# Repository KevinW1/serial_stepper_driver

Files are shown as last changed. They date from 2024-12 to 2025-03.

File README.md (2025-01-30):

# serial_stepper_driver
Simple stepper motor driver that can be controlled via serial communication.

Most existing drivers I found did not support 3 switch or analog inputs, so I created this.

Mouser parts:
https://www.mouser.com/ProjectManager/ProjectDetail.aspx?AccessID=6cd5e76669

Micro:
https://www.pjrc.com/store/teensy40.html

Driver:
https://www.pololu.com/product/3768

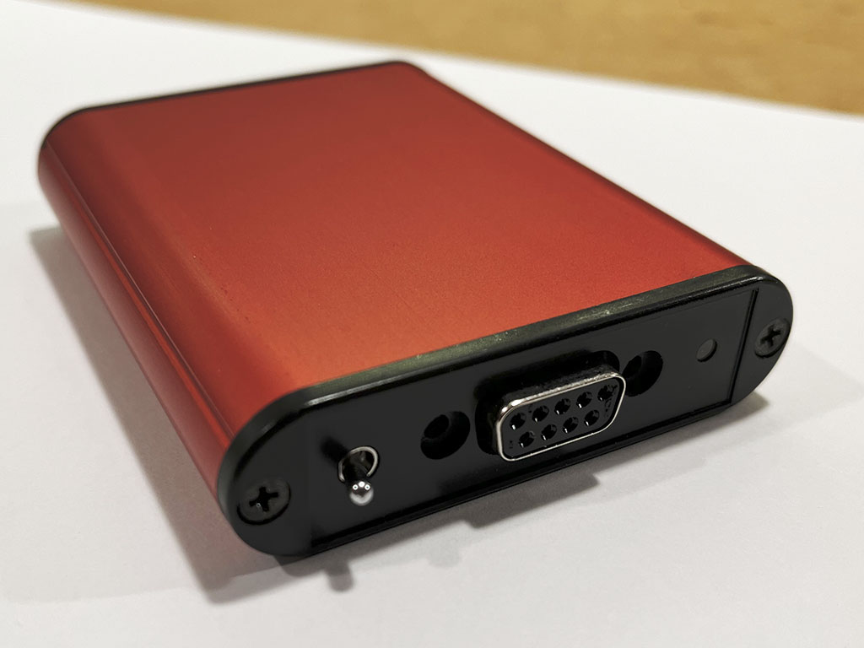
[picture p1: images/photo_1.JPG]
Finished Assembly
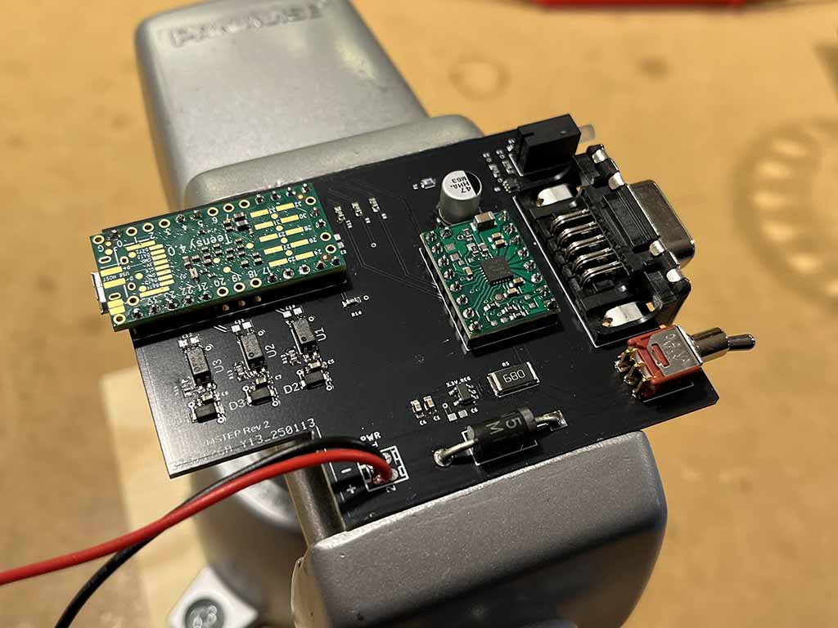
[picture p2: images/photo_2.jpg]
Board
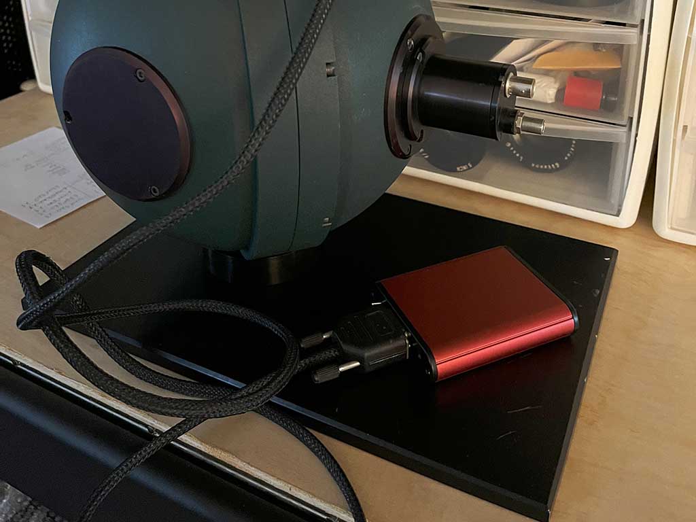
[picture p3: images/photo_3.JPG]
Application
|  |  |  |
|---|---|---|

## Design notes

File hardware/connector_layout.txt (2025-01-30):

1 B1
2 B2
3 A2
4 A1
5 GND
6 PWR (opto, hall sensor)
7 Lim1
8 Lim2
9 Home

gnd A1  A2  B1  B2
5   4   3   2   1
  6   7   8   9
  3.3 L1  L2  Home

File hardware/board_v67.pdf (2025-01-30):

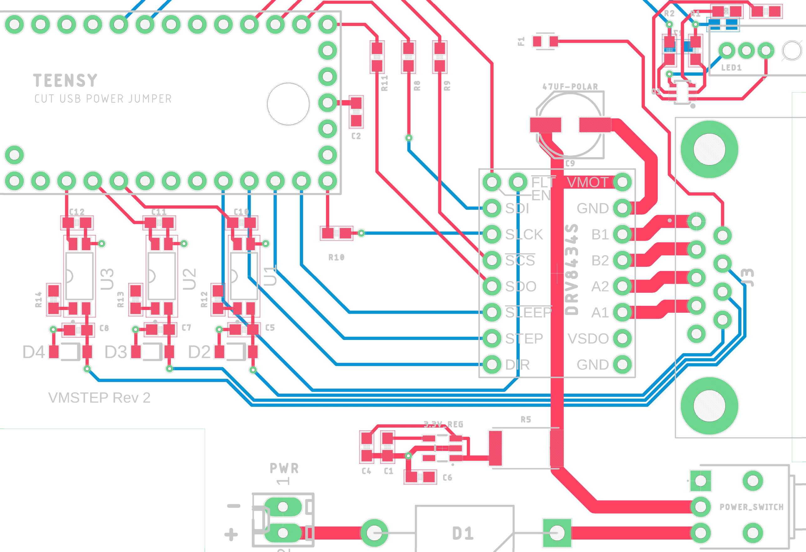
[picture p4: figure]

2

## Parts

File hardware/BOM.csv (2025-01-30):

SERIAL STEPPER DRIVER
https://www.mouser.com/ProjectManager/ProjectDetail.aspx?AccessID=6cd5e76669
Mouser # | Mfr. # | Manufacturer | Description | Order Qty. | Price (USD) | Ext.: (USD)
279-352268RJT | 352268RJT | TE Connectivity | Thick Film Resistors - SMD 3522 68R 5% 3W | 1 | $0.82 | $0.82
757-TLP291GBSE | TLP291(GB,SE | Toshiba | Transistor Output Optocouplers Gen Purp 1-Circuit 50mA 80V 3750Vrms | 3 | $0.48 | $1.44
576-SMF3.3 | SMF3.3 | Littelfuse | ESD Protection Diodes / TVS Diodes 200W 3.3V 5% Uni-directional | 3 | $0.45 | $1.35
80-C0603C104K5RAUTO | C0603C104K5RACAUTO | KEMET | Multilayer Ceramic Capacitors MLCC - SMD/SMT 50V 0.1uF X7R 0603 10% AEC-Q200 | 4 | $0.11 | $0.44
603-RC0603FR-07220RL | RC0603FR-07220RL | YAGEO | Thick Film Resistors - SMD 220 Ohms 100mW 0603 1% | 5 | $0.10 | $0.50
530-C2Q250 | C2Q 250 | Bel | Surface Mount Fuses Fuse | 2 | $0.29 | $0.58
603-RC0603FR-0768RL | RC0603FR-0768RL | YAGEO | Thick Film Resistors - SMD 68 Ohms 100mW 0603 1% | 4 | $0.10 | $0.40
863-MBT3904DW1T1G | MBT3904DW1T1G | onsemi | Bipolar Transistors - BJT 200mA 60V Dual NPN | 1 | $0.16 | $0.16
603-RC0603FR-0710KL | RC0603FR-0710KL | YAGEO | Thick Film Resistors - SMD 10 kOhms 100mW 0603 1% | 2 | $0.10 | $0.20
701-SPX3819M5-L-33TR | SPX3819M5-L-3-3/TR | MaxLinear | LDO Voltage Regulators 500mA LOW NOISE LDO | 1 | $0.45 | $0.45
80-C0603C103K5R7411 | C0603C103K5RAC7411 | KEMET | Multilayer Ceramic Capacitors MLCC - SMD/SMT 50V 0.01uF X7R 0603 10% | 1 | $0.10 | $0.10
603-RC0603FR-07100KL | RC0603FR-07100KL | YAGEO | Thick Film Resistors - SMD 100 kOhms 100mW 0603 1% | 2 | $0.10 | $0.20
612-200-A2262 | 200MSP1T2B2M6RE | E-Switch | Toggle Switches SPDT ON-ON PC MNT | 1 | $3.99 | $3.99
617-09661526615 | 9661526615 | HARTING | D-Sub Standard Connectors DSUB SV FEM SSDP ANG36-254 09P | 1 | $5.56 | $5.56
490-PJ-064A | PJ-064A | Same Sky | DC Power Connectors Power Jacks | 1 | $2.61 | $2.61
667-EEE-HA1H470XP | EEE-HA1H470XP | Panasonic | Aluminum Electrolytic Capacitors - SMD 47uF 50V | 1 | $0.38 | $0.38
546-1455B802RD | 1455B802RD | Hammond | Enclosures, Boxes, & Cases Alum w/Plastic Ends 3.15x2.82x.75" Red | 1 | $11.92 | $11.92
604-WP42WUM/EGW | WP42WUM/EGW | Kingbright | LED Circuit Board Indicators Red Grn 625 568nm White Diffused | 1 | $1.02 | $1.02
511-1N5822 | 1N5822 | STMicroelectronics | Schottky Diodes & Rectifiers Vr/40V Io/3A BULK | 1 | $0.32 | $0.32
Non-mouser
Teensy 4.0 dev board | TEENSY40 | PJRC | https://www.pjrc.com/store/teensy40.html | 1 | $23.80 | $23.80
SPI Stepper Motor Driver Carrier | DRV8434S | Pololu | https://www.pololu.com/product/3768 | 1 | $12.95 | $12.95
 |  |  |  |  | TOTAL | $69.19

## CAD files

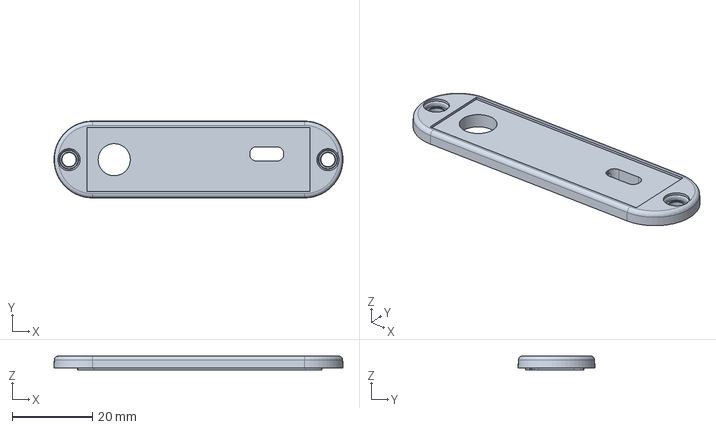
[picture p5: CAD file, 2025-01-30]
hardware/enclosure_back.step
72.0 x 19.1 x 3.50 mm

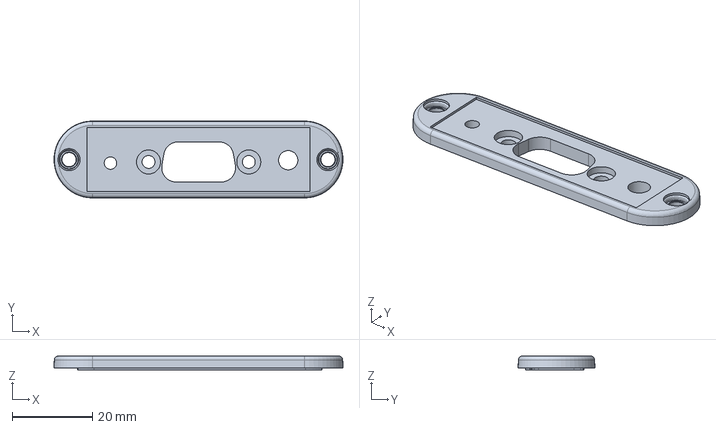
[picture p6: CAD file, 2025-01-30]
hardware/enclosure_front.step
72.0 x 19.1 x 3.50 mm

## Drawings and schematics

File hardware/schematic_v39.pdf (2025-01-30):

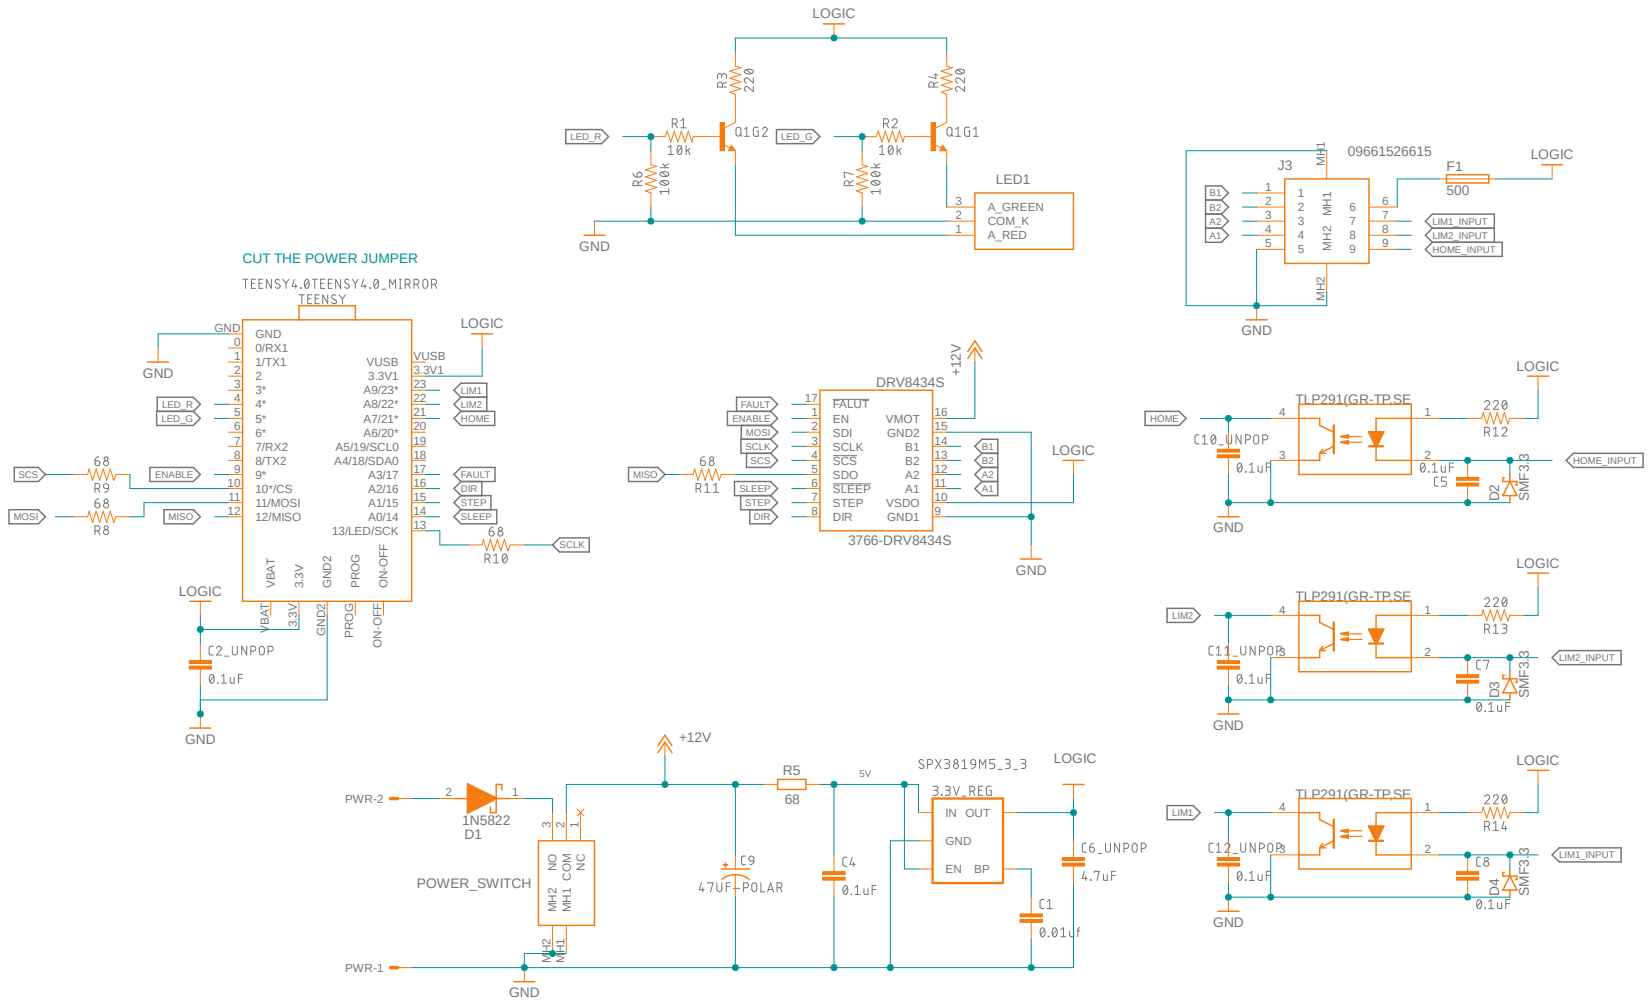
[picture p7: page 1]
GND; 3766-DRV8434S; GND +12V; +12V GND; LOGIC; LOGIC GND; SMF3.3 SMF3.3 SMF3.3; LED1 A_RED 1; COM_K 2; A_GREEN 3; POWER_SWITCH; 1 COM; DRV8434S; SDI 2; SCLK 3; SCS 4; SDO 5; SLEEP 6; STEP 7; DIR 8; GND1; 9 VSDO; 14 GND2; 15 VMOT; 16 FALUT 17; PWR-1 PWR-2; GND GND; VBAT VBAT; 17 A4/18/SDA0; 18 A5/19/SCL0; 10*/CS 10 11/MOSI 11 12/MISO 12; 13/LED/SCK; 13 VUSB; VUSB; PROG PROG GND² GND²; ON⁻OFF ON⁻OFF; IN OUT R5; STEP; STEP DIR; DIR; SCLK; SCS; B2 SLEEP; SLEEP; ENABLE; LIM1; LIM2; LED_G; HOME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

LOGIC GND GND

9 MH¹ MH¹ MH² MH²

TLP291(GR-TP,SE

EN BP GND

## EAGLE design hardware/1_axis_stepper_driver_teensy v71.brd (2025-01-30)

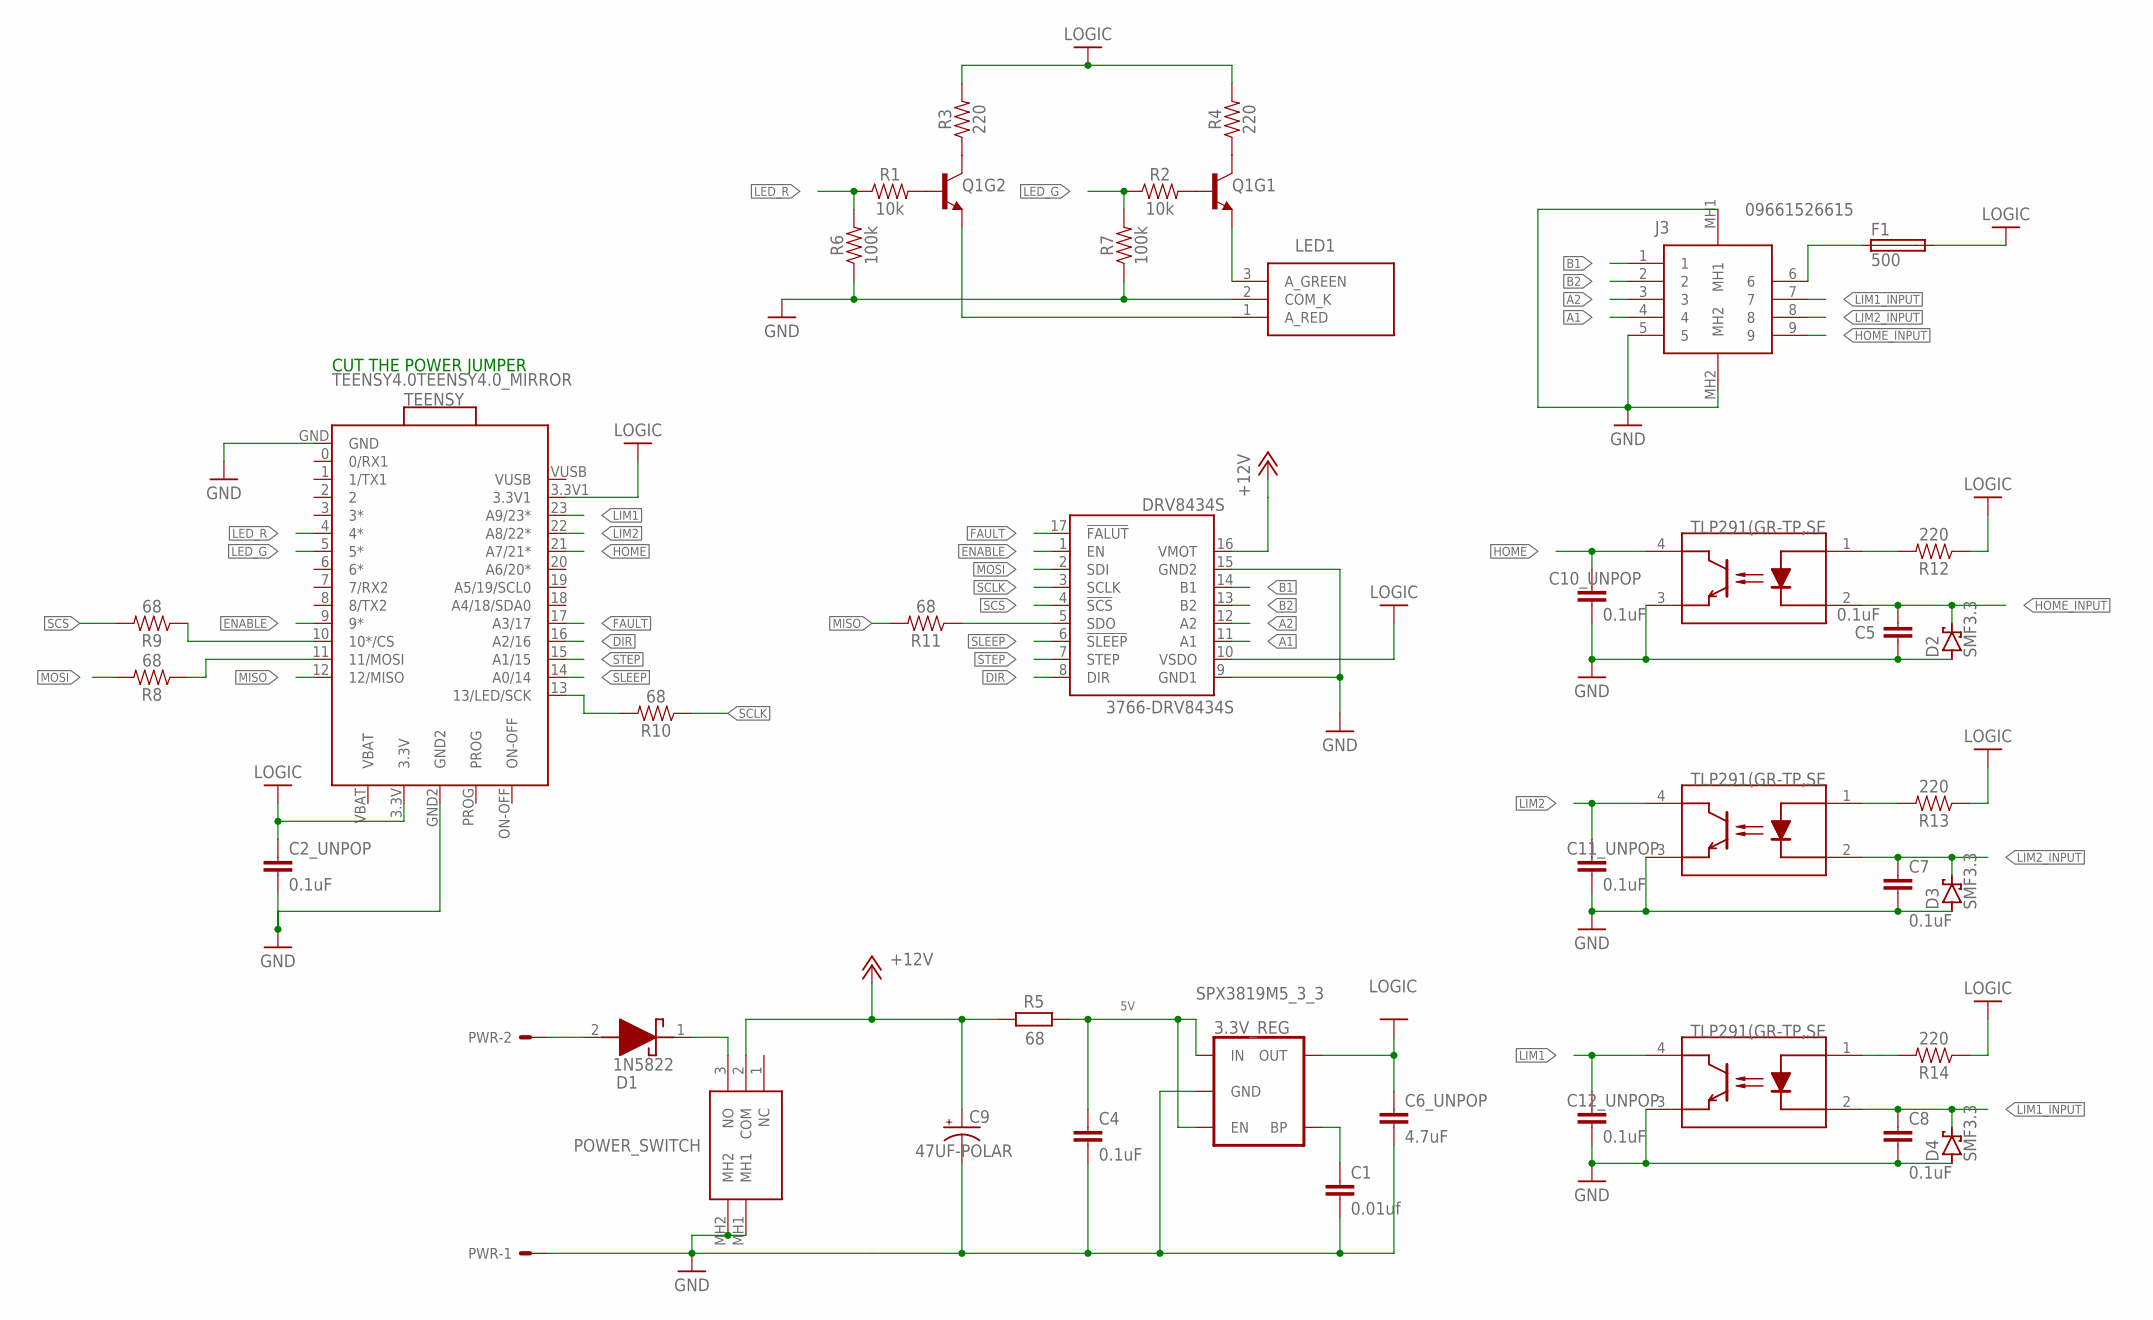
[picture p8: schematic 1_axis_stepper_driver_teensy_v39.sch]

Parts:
3.3V_REG: SPX3819M5_3_3; SOT23-5
C1: 0.01uf; 0603
C2_UNPOP, C4, C5, C7, C8, C10_UNPOP, C11_UNPOP, C12_UNPOP: 0.1uF; 0603
C6_UNPOP: 4.7uF; 0603
C9: 47UF-POLAR; PANASONIC_D
D1: 1N5822; DIOAD3070W130L950D530
D2, D3, D4: SMF3.3; SOD123FL
DRV8434S: 3766-DRV8434S; DRV8434S
F1: 500; FUSC1608X60N
J3: 09661526615
LED1: WP42WUM_EGW; WP42WUMEGW
POWER_SWITCH: 200MSP1T2B2M6RE
PWR: 22-27-2021-02; 6410-02
Q1: TRANS_NPN_DUAL-MBT3904DW1T1; SC70-6
R1, R2: 10k; 0603
R3, R4, R12, R13, R14: 220; 0603
R5: 68; RESC6332X71
R6, R7: 100k; 0603
R8, R9, R10, R11: 68; 0603
TEENSY: TEENSY4.0TEENSY4.0_MIRROR; TEENSY4.0_MIRROR
U1, U2, U3: TLP291(GR-TP,SE

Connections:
5V: 3.3V_REG.1 (IN), 3.3V_REG.3 (EN), C4.1, R5.2
+12V: C9.+, DRV8434S.16 (VMOT), POWER_SWITCH.2 (COM), R5.1
A1: DRV8434S.11 (A1), J3.4
A2: DRV8434S.12 (A2), J3.3
B1: DRV8434S.14 (B1), J3.1
B2: DRV8434S.13 (B2), J3.2
DCIN: D1.2 (A), PWR.2
DCSAFE: D1.1 (K), POWER_SWITCH.3 (NO)
DIR: DRV8434S.8 (DIR), TEENSY.16 (A2/16)
ENABLE: DRV8434S.1 (EN), TEENSY.9 (9*)
FAULT: DRV8434S.17 (!FALUT), TEENSY.17 (A3/17)
GND: 3.3V_REG.2 (GND), C1.2, C2_UNPOP.2, C4.2, C5.2, C6_UNPOP.2, C7.2, C8.2, C9.-, C10_UNPOP.2, C11_UNPOP.2, C12_UNPOP.2, D2.A, D3.A, D4.A, DRV8434S.9 (GND1), DRV8434S.15 (GND2), J3.5, J3.MH1, J3.MH2, LED1.2 (COM_K), POWER_SWITCH.MH1, POWER_SWITCH.MH2, PWR.1, R6.1, R7.1, TEENSY.GND, TEENSY.GND2, U1.3 (EMITTER), U2.3 (EMITTER), U3.3 (EMITTER)
HOME: C10_UNPOP.1, TEENSY.21 (A7/21*), U1.4 (COLLECTOR)
HOME_INPUT: C5.1, D2.C, J3.9, U1.2 (CATHODE)
LED_G: R2.1, R7.2, TEENSY.5 (5*)
LED_R: R1.1, R6.2, TEENSY.4 (4*)
LIM1: C12_UNPOP.1, TEENSY.23 (A9/23*), U3.4 (COLLECTOR)
LIM1_INPUT: C8.1, D4.C, J3.7, U3.2 (CATHODE)
LIM2: C11_UNPOP.1, TEENSY.22 (A8/22*), U2.4 (COLLECTOR)
LIM2_INPUT: C7.1, D3.C, J3.8, U2.2 (CATHODE)
LOGIC: 3.3V_REG.5 (OUT), C2_UNPOP.1, C6_UNPOP.1, DRV8434S.10 (VSDO), F1.2, R3.2, R4.2, R12.1, R13.1, R14.1, TEENSY.3.3V, TEENSY.3.3V1
MISO: R11.2, TEENSY.12 (12/MISO)
MOSI: DRV8434S.2 (SDI), R8.2
unnamed: Q1.6 (C), R3.1
unnamed: LED1.1 (A_RED), Q1.1 (E)
unnamed: Q1.2 (B), R1.2
unnamed: Q1.5 (B), R2.2
unnamed: Q1.3 (C), R4.1
unnamed: LED1.3 (A_GREEN), Q1.4 (E)
unnamed: F1.1, J3.6
unnamed: 3.3V_REG.4 (BP), C1.1
unnamed: R8.1, TEENSY.11 (11/MOSI)
unnamed: R9.1, TEENSY.10 (10*/CS)
unnamed: R10.2, TEENSY.13 (13/LED/SCK)
unnamed: DRV8434S.5 (SDO), R11.1
unnamed: R12.2, U1.1 (ANODE)
unnamed: R13.2, U2.1 (ANODE)
unnamed: R14.2, U3.1 (ANODE)
SCLK: DRV8434S.3 (SCLK), R10.1
SCS: DRV8434S.4 (!SCS), R9.2
SLEEP: DRV8434S.6 (!SLEEP), TEENSY.14 (A0/14)
STEP: DRV8434S.7 (STEP), TEENSY.15 (A1/15)
VBAT: TEENSY.VBAT
VUSB: TEENSY.VUSB

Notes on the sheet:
CUT THE POWER JUMPER

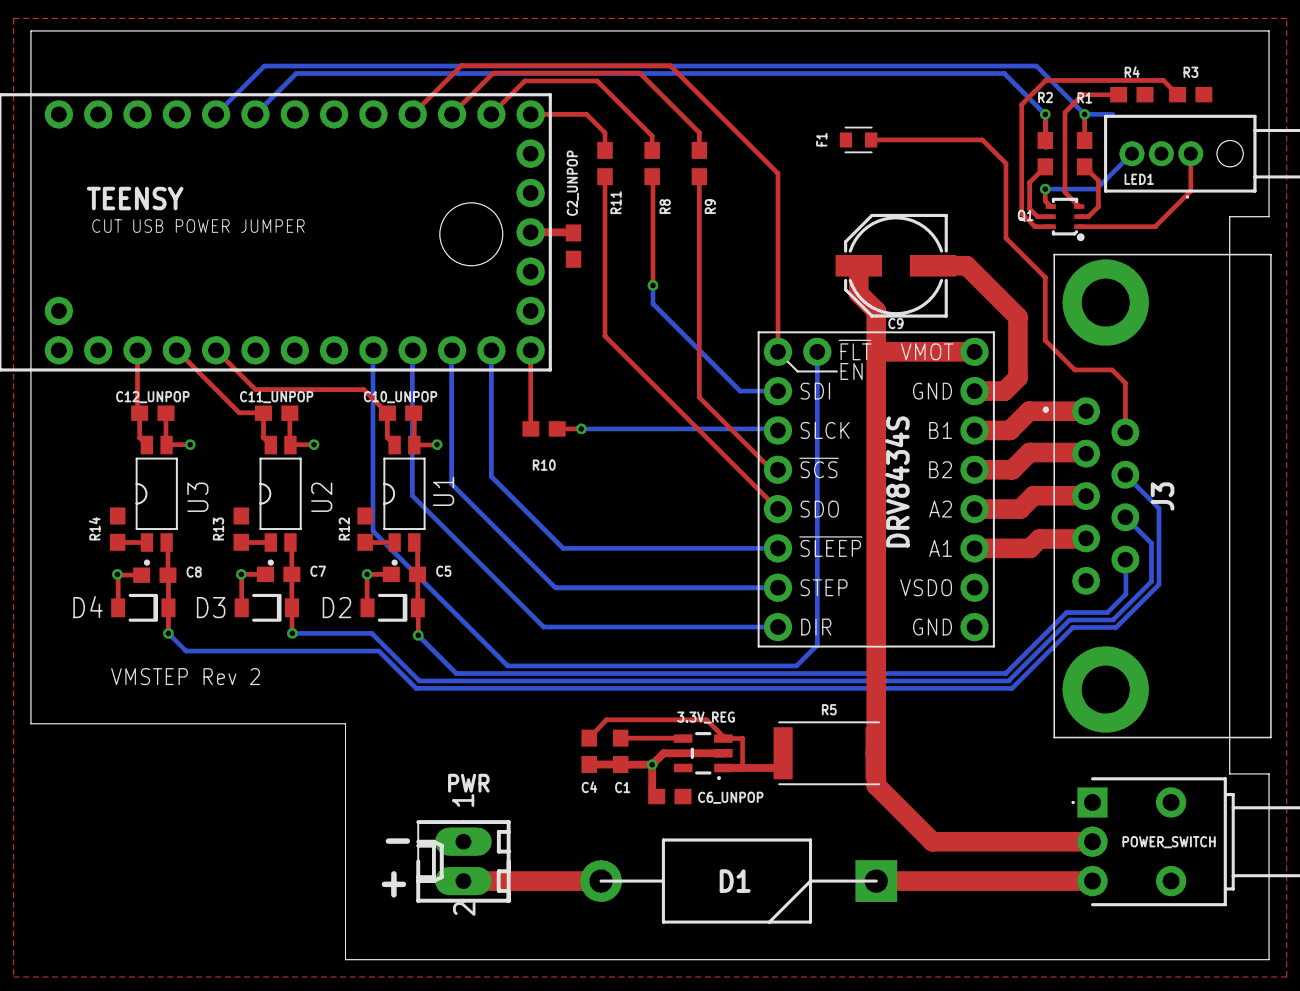
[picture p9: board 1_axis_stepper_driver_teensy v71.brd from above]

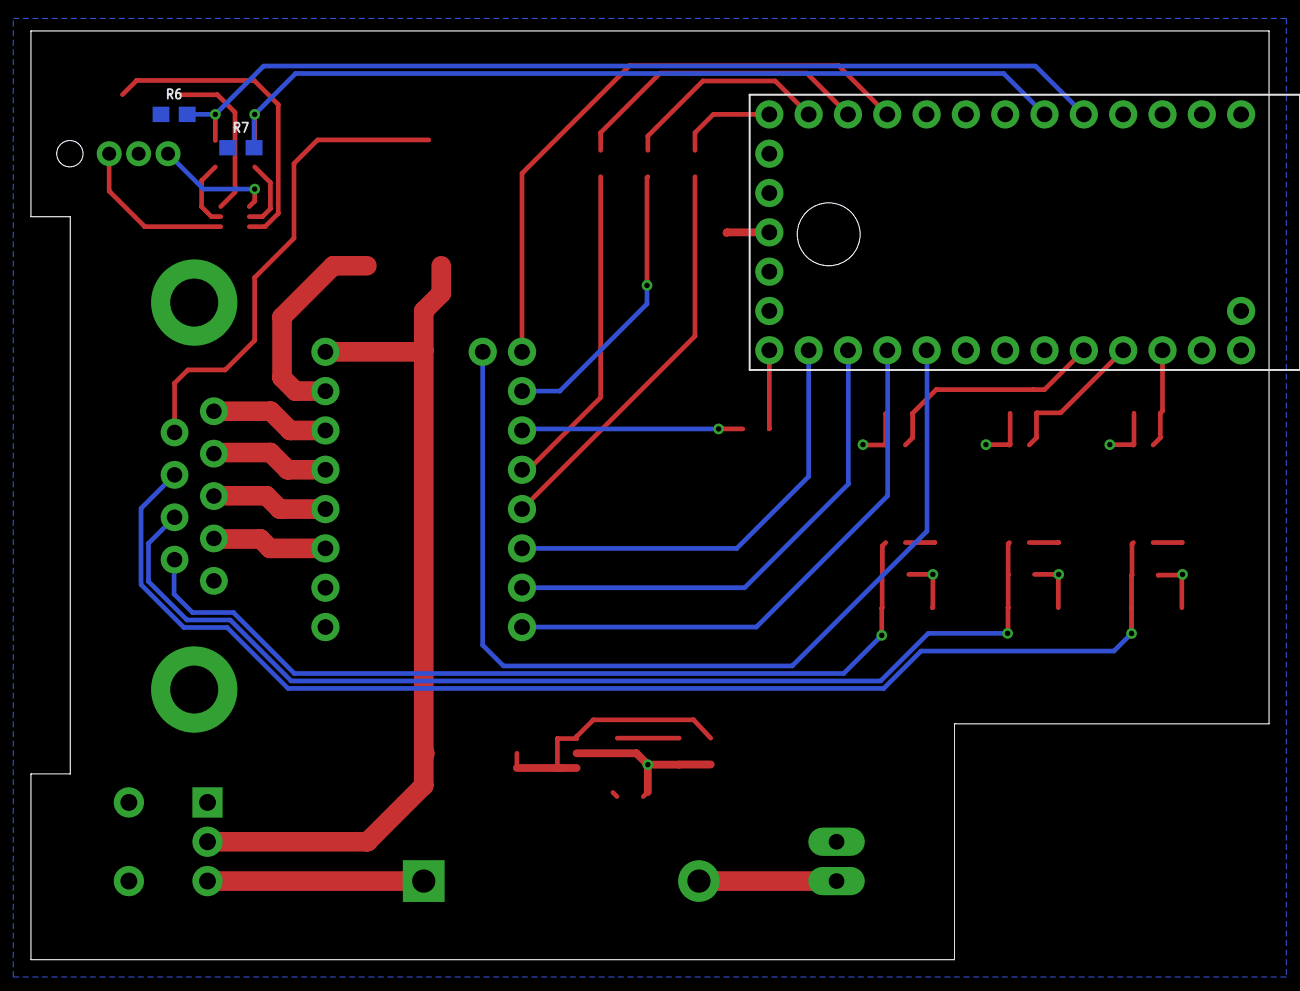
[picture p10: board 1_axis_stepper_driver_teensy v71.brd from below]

Board: 2 copper layers, 80.0 x 60.0 mm, 41 parts (2 on the bottom side), 42 nets.

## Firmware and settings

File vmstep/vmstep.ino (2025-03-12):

#include "Comms.h"
#include "Settings.h"
#include "Motor.h"
#include "name.h"
#include <limits.h>

// pin definitions
// Motor
static constexpr byte PIN_SLEEP = 14;  //6;
static constexpr byte PIN_STEP = 15;   //7;
static constexpr byte PIN_DIR = 16;    //8;
static constexpr byte PIN_ENABLE = 9;
static constexpr byte PIN_SCS = 10;
static constexpr byte PIN_FAULT = 17;
// system
static constexpr byte PIN_LED_R = 4;
static constexpr byte PIN_LED_G = 5;
// Sensors
static constexpr byte PIN_LIM1 = 23;  //16;
static constexpr byte PIN_LIM2 = 22;  //15;
static constexpr byte PIN_HOME = 21;  //14;
// system control
static constexpr uint16_t LED_PULSE_PERIOD = 2000;  // 2 second cycle


enum class Mode {
    idle,    // waiting for commands, full current
    sleep,   // waiting for commands, low current
    moving,  // moving to a position
    homing,  // moving, waiting for home sensor
    fault    // Stop all operations
};
Mode device_mode = Mode::idle;

unsigned long idle_time = 0;  // time controler entered idle state

union {
    long value;
    uint8_t bytes[4];
} position;

Settings_union settings;
SerialTransciever Comms;
Motor motor(PIN_SCS, PIN_STEP, PIN_DIR, PIN_ENABLE, PIN_SLEEP, settings);

void setup() {
    reset_controller();
}

void reset_controller() {
    init_serial();
    // Check if settings are valid
    if (!validate_settings(settings)) {
        Comms.send(REPLY_FAULT, FAULT_INVALID_PARAMETERS);
        enter_fault_state();
        return;
    }

    // sensors
    pinMode(PIN_LIM1, INPUT_PULLUP);
    pinMode(PIN_LIM2, INPUT_PULLUP);
    pinMode(PIN_HOME, INPUT_PULLUP);
    // driver
    pinMode(PIN_FAULT, INPUT_PULLUP);  // logic low = fault
    // led
    pinMode(PIN_LED_R, OUTPUT);
    pinMode(PIN_LED_G, OUTPUT);

    motor.init();

    // Check communication with driver
    if (!motor.update_settings()) {
        enter_fault_state();
        Comms.send(REPLY_FAULT, FAULT_DRIVER_SYNC);
        return;
    }

    enter_idle_state();
    Comms.send(REPLY_ACK);
}

// State control functions
void enter_idle_state() {
    // if (device_mode == Mode::fault) return;
    device_mode = Mode::idle;
    idle_time = millis();
    analogWrite(PIN_LED_G, 128);
    analogWrite(PIN_LED_R, 0);
}

void enter_sleep_state() {
    // if (device_mode == Mode::fault) return;
    device_mode = Mode::sleep;
    // apply sleep current to motor
    motor.set_current(settings.data.sleep_current);
    analogWrite(PIN_LED_R, 0);
    analogWrite(PIN_LED_G, 128);
}

void enter_moving_state() {
    // if (device_mode == Mode::fault) return;
    device_mode = Mode::moving;
    // apply run current to motor
    motor.set_current(settings.data.run_current);
    analogWrite(PIN_LED_G, 255);
    analogWrite(PIN_LED_R, 0);
}

void enter_homing_state() {
    // if (device_mode == Mode::fault) return;
    device_mode = Mode::homing;
    // apply run current to motor
    motor.set_current(settings.data.run_current);
    analogWrite(PIN_LED_G, 128);
    analogWrite(PIN_LED_R, 128);
}

void enter_fault_state() {
    device_mode = Mode::fault;
    motor_hard_stop();
    motor.disable_driver();
    analogWrite(PIN_LED_G, 0);
    analogWrite(PIN_LED_R, 255);
}

// Motor command functions
void motor_goto(byte data[]) {
    memcpy(position.bytes, data + 1, sizeof(position.bytes));
    motor.goto_pos(position.value);
    enter_moving_state();
    Comms.send(REPLY_ACK, position.bytes, sizeof(position.bytes));
}

void motor_home(byte data[]) {
    if (!settings.data.flags.enable_home) {
        Comms.send(REPLY_FAULT, FAULT_HOME);
        enter_fault_state();
        return;
    }
    // Set homing direction from byte 1
    long homing_pos = LONG_MAX;
    if (!data[1]) {
        homing_pos = -LONG_MAX;
    }
    // Reset internal position so long_max doesn't overflow
    motor.reset_position();
    position.value = 0;  // Reset our position tracking
    motor.goto_pos(homing_pos);
    enter_homing_state();
    Comms.send(REPLY_ACK);
    // limits are checks in the main loop
}

void motor_stop() {
    motor.stop();
    enter_moving_state();  //decel
    Comms.send(REPLY_ACK);
}

void motor_hard_stop() {
    motor.hard_stop();
    enter_idle_state();
    Comms.send(REPLY_ACK);
}

void motor_enable() {
    motor.enable_driver();
    enter_idle_state();
    Comms.send(REPLY_ACK);
}

void motor_disable() {
    motor.disable_driver();
    enter_idle_state();
    Comms.send(REPLY_ACK);
}

void motor_reset_position() {
    if (device_mode != Mode::idle && device_mode != Mode::sleep) {
        Comms.send(REPLY_FAULT, FAULT_NACK);
        return;
    }
    motor.reset_position();
    position.value = 0;  // Reset our position tracking
    enter_idle_state();
    Comms.send(REPLY_ACK);
}

// Controller functions

void controller_echo() {
    Comms.send(REPLY_ACK, REPLY_ECHO);
}

void update_parameters(byte data[], size_t length) {
    // First byte is always the command byte
    if (length - 1 == sizeof(settings.bytes)) {
        // Validate before applying
        Settings_union temp_settings;
        memcpy(temp_settings.bytes, data + 1, sizeof(settings.bytes));
        if (!validate_settings(temp_settings)) {
            Comms.send(REPLY_FAULT, FAULT_INVALID_PARAMETERS);
            return;
        }
        // Apply the settings
        memcpy(settings.bytes, data + 1, sizeof(settings.bytes));
        if (!motor.update_settings()) {
            Comms.send(REPLY_FAULT, FAULT_DRIVER_SYNC);
            enter_fault_state();
            return;
        }
        Comms.send(REPLY_ACK, "Settings updated");
    } else {
        Comms.send(REPLY_FAULT, FAULT_INVALID_PARAMETERS);
    }
}

void controller_query(byte data[]) {
    byte query_type = data[1];
    switch (query_type) {
        case QUERY_MODEL_NO:
            {
                static const char product[] = PRODUCT_NAME;
                Comms.send(REPLY_ACK, (byte*)product, PRODUCT_NAME_LEN);
                break;
            }
        case QUERY_SERIAL_NO:
            {
                static const char serial_num[] = SERIAL_NUMBER;
                Comms.send(REPLY_ACK, (byte*)serial_num, SERIAL_NUMBER_LEN);
                break;
            }
        case QUERY_FIRMWARE:
            {
                static const char firmware_ver[] = FIRMWARE_VERSION;
                Comms.send(REPLY_ACK, (byte*)firmware_ver, FIRMWARE_VERSION_LEN);
                break;
            }
        case QUERY_PARAMETERS:
            Comms.send(REPLY_ACK, settings.bytes, sizeof(settings.bytes));
            break;
        case QUERY_POSITION:
            {
                position.value = motor.position();  // Update position from motor
                Comms.send(REPLY_ACK, position.bytes, sizeof(position.bytes));
                break;
            }
        case QUERY_MODE:
            {
                byte mode = static_cast<byte>(device_mode);
                Comms.send(REPLY_ACK, &mode, 1);
                break;
            }
        case QUERY_FAULT_REGS:
            {
                const std::array<byte, 3>& fault_registers = motor.get_fault_registers();
                Comms.send(REPLY_ACK, fault_registers.data(), 3);  // Send all 3 registers
                break;
            }

        default:
            Comms.send(REPLY_FAULT, FAULT_NACK);
    }
}

bool fault_allowed_command(byte cmd) {
    switch (cmd) {
        case CMD_RESET: [[fallthrough]];
        case CMD_QUERY: [[fallthrough]];
        case CMD_ECHO:
            return true;
        default:
            return false;
    }
}

void process_message(byte data[], size_t length) {
    byte cmd = data[0];

    // Check if command allowed in fault state
    if (device_mode == Mode::fault && !fault_allowed_command(cmd)) {
        Comms.send(REPLY_FAULT, FAULT_NACK);
        return;
    }

    switch (cmd) {
        case CMD_GOTO: motor_goto(data); break;
        case CMD_STOP: motor_stop(); break;
        case CMD_HOME: motor_home(data); break;
        case CMD_RESET: reset_controller(); break;
        case CMD_QUERY: controller_query(data); break;
        case CMD_UPDATE_PARAMETERS: update_parameters(data, length); break;
        case CMD_ECHO: controller_echo(); break;
        case CMD_ENABLE: motor_enable(); break;
        case CMD_DISABLE: motor_disable(); break;
        case CMD_RESET_POSITION: motor_reset_position(); break;
        default:
            Comms.send(REPLY_FAULT, FAULT_NACK);
    }
}

void check_sensors() {
    // Check driver fault (active low)
    if (digitalRead(PIN_FAULT) == LOW && device_mode != Mode::fault) {
        // Create fault report array: [FAULT_DRIVER, fault_reg, diag1_reg, diag2_reg]
        byte fault_data[4] = { FAULT_DRIVER };

        const std::array<byte, 3>& fault_registers = motor.get_fault_registers();
        memcpy(fault_data + 1, fault_registers.data(), 3);

        enter_fault_state();
        Comms.send(REPLY_FAULT, fault_data, sizeof(fault_data));
        return;
    }

    // check home
    if (settings.data.flags.enable_home && device_mode == Mode::homing) {
        if (digitalRead(PIN_HOME) == settings.data.flags.home_sig_polarity) {
            enter_idle_state();
            motor.reset_position();
            Comms.send(REPLY_DONE);
        }
    }
    // check lim 1
    if (settings.data.flags.enable_lim1) {
        if (digitalRead(PIN_LIM1) == settings.data.flags.lim1_sig_polarity) {
            enter_fault_state();
            Comms.send(REPLY_FAULT, FAULT_LIMT1);
        }
    }
    // check lim 2
    if (settings.data.flags.enable_lim2) {
        if (digitalRead(PIN_LIM2) == settings.data.flags.lim2_sig_polarity) {
            enter_fault_state();
            Comms.send(REPLY_FAULT, FAULT_LIMT2);
        }
    }
}

// Loop activities

void idle() {
    if ((millis() - idle_time) > (settings.data.sleep_timeout * 10)) {
        enter_sleep_state();
    }
}

void sleeping() {
    // pulse led geen
    float phase = (float)((millis() % LED_PULSE_PERIOD) * 2 * PI) / LED_PULSE_PERIOD;
    byte brightness = (byte)(128 + 127 * sin(phase));
    analogWrite(PIN_LED_G, brightness);
}

void moving() {
    if (motor.steps_remaining() == 0) {
        position.value = motor.position();
        enter_idle_state();
        Comms.send(REPLY_DONE, position.bytes, sizeof(position.bytes));
    } else {
        motor.run();
    }
}

void homing() {
    if (motor.steps_remaining() == 0) {
        // home distance exceedd max position value.
        enter_fault_state();
        Comms.send(REPLY_FAULT, FAULT_HOME);
    } else {
        motor.run();
    }
}

void loop() {
    Comms.run(process_message);

    check_sensors();

    switch (device_mode) {
        case Mode::idle: idle(); break;
        case Mode::sleep: sleeping(); break;
        case Mode::moving: moving(); break;
        case Mode::homing: homing(); break;
        default: break;
    }
}

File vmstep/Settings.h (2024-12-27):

#ifndef Settings_h
#define Settings_h
#include <Arduino.h>

static constexpr uint8_t MicroStep1_100 = 0b0000;  // Full step with 100% current
static constexpr uint8_t MicroStep1 = 0b0001;      // Full step with 71% current
static constexpr uint8_t MicroStep2_NC = 0b0010;   // Non-circular 1/2 step
static constexpr uint8_t MicroStep2 = 0b0011;      // Circular 1/2 step
static constexpr uint8_t MicroStep4 = 0b0100;
static constexpr uint8_t MicroStep8 = 0b0101;
static constexpr uint8_t MicroStep16 = 0b0110;
static constexpr uint8_t MicroStep32 = 0b0111;
static constexpr uint8_t MicroStep64 = 0b1000;
static constexpr uint8_t MicroStep128 = 0b1001;
static constexpr uint8_t MicroStep256 = 0b1010;

struct __attribute__((packed)) Settings_struct {
    //motor control
    uint8_t run_current : 4;
    uint8_t sleep_current : 4;
    uint8_t microstep_res : 4;
    uint8_t reserved : 4;   // padding for alignment
    uint8_t sleep_timeout;  // 10s of ms

    //trajectory
    uint32_t top_speed;
    uint32_t acceleration;

    //limit switch flags packed into single byte
    struct {
        uint8_t enable_lim1 : 1;        // bit 0
        uint8_t enable_lim2 : 1;        // bit 1
        uint8_t enable_home : 1;        // bit 2
        uint8_t lim1_sig_polarity : 1;  // bit 3
        uint8_t lim2_sig_polarity : 1;  // bit 4
        uint8_t home_sig_polarity : 1;  // bit 5
        uint8_t reserved : 2;           // bits 6-7 reserved
    } flags;
};

union Settings_union {
    Settings_struct data{
        .run_current = 0b0000,         // run current (min)
        .sleep_current = 0b0000,       // sleep current (min)
        .microstep_res = MicroStep16,  // microstep res
        .sleep_timeout = 100,         // sleep timeout 1s
        .top_speed = 2000,           // top speed
        .acceleration = 4000,        // acceleration
        .flags = {
            // limit switch flags
            .enable_lim1 = 0,
            .enable_lim2 = 0,
            .enable_home = 0,
            .lim1_sig_polarity = 0,
            .lim2_sig_polarity = 0,
            .home_sig_polarity = 0,
            .reserved = 0 }
    };
    byte bytes[sizeof(Settings_struct)];
};

inline bool validate_settings(const Settings_union& settings) {
    // Nothing to validate yet
    return true;
}

#endif

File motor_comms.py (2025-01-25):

from __future__ import annotations

import logging
import struct
import time
from ctypes import Structure, Union, c_uint8, c_uint32, sizeof
from enum import Enum
from types import TracebackType
from typing import Optional, Type

import serial
from serial.tools.list_ports import comports

logger = logging.getLogger(__name__)

MANUFACTURER = "VIRTUALMATTER"
PRODUCT = "VMSTEP"

LINE_BEGIN = b"["
LINE_END = b"]"

FAULT_MESSAGES = {
    7: "FAULT pin active",
    6: "SPI protocol error",
    5: "Supply undervoltage lockout",
    4: "Charge pump undervoltage",
    3: "Overcurrent",
    2: "Motor stall",
    1: "Thermal flag",
    0: "Open load",
}

DIAG1_MESSAGES = {
    7: "Overcurrent on BOUT low-side FET 2",
    6: "Overcurrent on BOUT high-side FET 2",
    5: "Overcurrent on BOUT low-side FET 1",
    4: "Overcurrent on BOUT high-side FET 1",
    3: "Overcurrent on AOUT low-side FET 2",
    2: "Overcurrent on AOUT high-side FET 2",
    1: "Overcurrent on AOUT low-side FET 1",
    0: "Overcurrent on AOUT high-side FET 1",
}

DIAG2_MESSAGES = {
    # 7: "Reserved",
    6: "Overtemperature warning",
    5: "Overtemperature shutdown",
    4: "Stall detection learning successful",
    3: "Motor stall detected",
    # 2: "Reserved",
    1: "Open load on BOUT",
    0: "Open load on AOUT",
}


class Cmd(Enum):
    GOTO = b"G"
    STOP = b"S"
    HOME = b"H"
    RESET = b"R"
    QUERY = b"Q"
    UPDATE_PARAMETERS = b"P"
    ECHO = b"E"
    ENABLE = b"Y"
    DISABLE = b"X"
    RESET_POSITION = b"Z"


class Query(Enum):
    MODEL_NO = b"M"
    SERIAL_NO = b"S"
    FIRMWARE = b"W"
    PARAMETERS = b"P"
    FAULTS = b"F"
    POSITION = b"X"
    MODE = b"T"
    FAULT_REGS = b"R"


class DeviceMode(Enum):
    IDLE = 0
    SLEEP = 1
    MOVING = 2
    HOMING = 3
    FAULT = 4


class Reply(Enum):
    ACK = b"A"
    DONE = b"D"
    FAULT = b"F"
    ECHO = b"E"


class Fault(Enum):
    NACK = b"N"
    DRIVER = b"D"
    INVALID_PARAMETERS = b"P"
    DRIVER_SYNC = b"Y"
    LIMT1 = b"L"
    LIMT2 = b"K"
    HOME = b"H"


class Microsteps(Enum):
    MicroStep1_100 = 0b0000
    MicroStep1 = 0b0001
    MicroStep2_NC = 0b0010
    MicroStep2 = 0b0011
    MicroStep4 = 0b0100
    MicroStep8 = 0b0101
    MicroStep16 = 0b0110
    MicroStep32 = 0b0111
    MicroStep64 = 0b1000
    MicroStep128 = 0b1001
    MicroStep256 = 0b1010


class SettingsFlags(Structure):
    """Maps to the flags bitfield struct in Settings_struct"""

    _fields_ = [
        ("enable_lim1", c_uint8, 1),  # bit 0
        ("enable_lim2", c_uint8, 1),  # bit 1
        ("enable_home", c_uint8, 1),  # bit 2
        ("lim1_sig_polarity", c_uint8, 1),  # bit 3
        ("lim2_sig_polarity", c_uint8, 1),  # bit 4
        ("home_sig_polarity", c_uint8, 1),  # bit 5
        ("reserved", c_uint8, 2),  # bits 6-7
    ]


class SettingsStruct(Structure):
    """Maps to Settings_struct in C++"""

    _pack_ = 1  # Match __attribute__((packed))
    _fields_ = [
        ("run_current", c_uint8, 4),
        ("sleep_current", c_uint8, 4),
        ("microstep_res", c_uint8, 4),
        ("reserved", c_uint8, 4),  # padding for algiment
        ("sleep_timeout", c_uint8),  # 10s of ms
        ("top_speed", c_uint32),
        ("acceleration", c_uint32),
        ("flags", SettingsFlags),  # bitfield struct
    ]


class Settings(Union):
    """Maps to Settings_union in C++"""

    _pack_ = 1
    _fields_ = [("data", SettingsStruct), ("bytes", c_uint8 * sizeof(SettingsStruct))]

    def __str__(self) -> str:
        """Return human-readable settings string"""
        flags = self.data.flags
        return (
            f"\nMotor Settings:\n"
            f"-------------\n"
            f"Step Current     : {self.data.run_current}/15\n"
            f"Sleep Current    : {self.data.sleep_current}/15\n"
            f"Microstep Res    : {Microsteps(self.data.microstep_res).name}\n"
            f"Sleep Timeout    : {self.data.sleep_timeout*10}ms\n"
            f"Maximum Speed    : {self.data.top_speed} steps/s\n"
            f"Acceleration     : {self.data.acceleration} steps/s²\n"
            f"\nLimit Switches:\n"
            f"-------------\n"
            f"Limit 1    : {'Enabled' if flags.enable_lim1 else 'Disabled'} "
            f"({'Active-High' if flags.lim1_sig_polarity else 'Active-Low'})\n"
            f"Limit 2    : {'Enabled' if flags.enable_lim2 else 'Disabled'} "
            f"({'Active-High' if flags.lim2_sig_polarity else 'Active-Low'})\n"
            f"Home       : {'Enabled' if flags.enable_home else 'Disabled'} "
            f"({'Active-High' if flags.home_sig_polarity else 'Active-Low'})"
        )


class VMSTEP:
    VMSTEP_SERIAL_KWARGS = {
        "baudrate": 19200,
        "parity": serial.PARITY_NONE,
        "stopbits": serial.STOPBITS_ONE,
        "bytesize": serial.EIGHTBITS,
        "timeout": 0.5,
    }

    @classmethod
    def discover(self, serial_number: Optional[str] = None) -> "VMSTEP":
        """Attempt automatic discovery of the VMSTEP serial port
        and return the VMSTEP object.

        Returns
        -------
        VMSTEP
            A successfully located VMSTEP object.

        Raises
        ------
        serial.SerialException
            If no serial port can be automatically linked.
        """

        port_list = comports()

        if len(port_list) == 0:
            raise serial.SerialException("No serial ports found on this machine")

        for p in port_list:
            if p.manufacturer != MANUFACTURER and p.product != PRODUCT:
                continue

            if not serial_number or p.serial_number == serial_number:
                serial_port = serial.Serial(p.device, **self.VMSTEP_SERIAL_KWARGS)
                serial_port.read_all()
                return VMSTEP(serial_port)
            else:
                continue

        raise serial.SerialException(
            """Could not connect to any devices.
                Check connection and power."""
        )

    def __init__(self, serial_port: str | serial.Serial = None):
        self.logger = logging.getLogger(__name__)
        if isinstance(serial_port, str):
            self._port = serial.Serial(serial_port, **self.VMSTEP_SERIAL_KWARGS)
        else:
            self._port = serial_port

    def __enter__(self) -> "VMSTEP":
        self.open()
        return self

    def __exit__(
        self,
        exc_type: Optional[Type[BaseException]],
        exc_val: Optional[BaseException],
        exc_tb: Optional[TracebackType],
    ) -> None:
        self.close()

    def _clear_buffer(self) -> None:
        self._port.read_all()

    def open(self) -> None:
        if isinstance(self._port, str):
            self._port = serial.Serial(self._port, **self.VMSTEP_SERIAL_KWARGS)
        self._clear_buffer()

    def close(self) -> None:
        self._port.close()
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

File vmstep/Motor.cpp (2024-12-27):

#include "Motor.h"
#include "Settings.h"

Motor::Motor(byte pin_cs, byte pin_step, byte pin_dir, byte pin_enable, byte pin_sleep, Settings_union &_settings)
    : PIN_CS(pin_cs),
      PIN_STEP(pin_step),
      PIN_DIR(pin_dir),
      PIN_ENABLE(pin_enable),
      PIN_SLEEP(pin_sleep),
      settings(&_settings),
      // init children.  AccelStepper for step rate, and DRV8434S for driver control.
      stepper{ AccelStepper::DRIVER, pin_step, pin_dir },
      driver{} {
}

void Motor::init() {
    SPI.begin();
    driver.setChipSelectPin(PIN_CS);

    pinMode(PIN_STEP, OUTPUT);
    pinMode(PIN_DIR, OUTPUT);
    pinMode(PIN_ENABLE, OUTPUT);
    pinMode(PIN_SLEEP, OUTPUT);

    digitalWrite(PIN_STEP, LOW);
    digitalWrite(PIN_DIR, LOW);
    digitalWrite(PIN_ENABLE, LOW); // high is enabled, low is disabled.
    digitalWrite(PIN_SLEEP, HIGH); // high is awake, low is sleep.

    delay(1);
    // Reset the driver to its default settings and clear latched fault conditions.
    // TODO: set better defaults in driver library
    driver.resetSettings();
    set_current(0b0000);  // min
    driver.clearFaults();
    driver.enableDriver();  // digital enable via SPI.
    disable_driver();   // physical disable via pin low.
}

void Motor::enable_driver() {
    digitalWrite(PIN_ENABLE, HIGH);
}

void Motor::disable_driver() {
    digitalWrite(PIN_ENABLE, LOW);
}

bool Motor::try_verify_settings() {
    // Accounts for processing times inside the driver chip.
    for(int i = 0; i < 10; i++) {
        if (driver.verifySettings()) {
            return true;
        }
        delay(1);
    }
    return false;
}

bool Motor::update_settings() {
    // update planner
    stepper.setMaxSpeed(settings->data.top_speed);
    stepper.setAcceleration(settings->data.acceleration);
    // driver update
    driver.setStepMode(static_cast<DRV8434SStepMode>(settings->data.microstep_res));
    return try_verify_settings();
}

bool Motor::set_current(uint8_t current) {
    // this is dynamically switched based on controller state.
    driver.setCurrent(current);
    return try_verify_settings();
}

void Motor::goto_pos(long steps) {
    stepper.move(steps);
}

void Motor::reset_position() {
    stepper.setCurrentPosition(0);
}

void Motor::run() {
    stepper.run();
}

void Motor::run_continuous() {
    stepper.runSpeed();
}

void Motor::stop() {
    // includes deceleration
    stepper.stop();
}

void Motor::hard_stop() {
    stepper.setCurrentPosition(stepper.targetPosition());
}

long Motor::position() {
    return stepper.currentPosition();
}

long Motor::steps_remaining() {
    return stepper.distanceToGo();
}

const std::array<byte, 3>& Motor::get_fault_registers() {
    fault_registers[0] = driver.readFault();
    fault_registers[1] = driver.readDiag1();
    fault_registers[2] = driver.readDiag2();
    return fault_registers;
}

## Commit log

2024-10-21 Add motor stop command
2024-11-30 Not working, homes too quickly and faults on startup sometimes
    [Comms.cpp, Comms.h, Motor.cpp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]
2024-12-19 Improved homing using accel
2024-12-22 Driver fault handling
2024-12-27 Fix microsteps, remove settings.cpp
    [Comms.h, Motor.cpp, Settings.h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]
2025-01-30 Add hardware files
    [1_axis_stepper_driver_teensy v71.brd, 1_axis_stepper_driver_teensy_v39.sch, BOM.csv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]
2025-01-30 Add Gerber files
2025-03-12 Zero motor before homing to prevent overflow
    [vmstep.ino]

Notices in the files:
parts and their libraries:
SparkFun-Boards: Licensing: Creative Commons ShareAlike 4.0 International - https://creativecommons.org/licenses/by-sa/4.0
